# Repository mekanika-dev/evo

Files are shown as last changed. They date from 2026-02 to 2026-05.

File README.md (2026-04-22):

# Evo CNC

> Evo is a versatile CNC milling machine that lets you explore different materials. Fast and easy to use, it's the ideal choice for hobbyists and occasional professionals.

- [Assembly Guide & Documentation](https://support.mekanika.io/products/evo-cnc)
- [Shop](https://www.mekanika.io/en/store/be/evo/)
- [Contact](https://www.mekanika.io/contact-us/)

Evo CNC Milling Machine

## Repository Structure

- **`bom/`** - Bill of Materials
- **`cad/`** - CAD files
- **`docs/`** - Documentation files

The Bill of Materials is available as a CSV file, which is dynamically updated from our ERP. We recommend using this **[web viewer](https://mekanika-dev.github.io/data-sync-actions/odoo/bom-viewer.html)** to browse its content.

All 3D assembly files are made in STEP format and compatible with many CAD software. Please note that you will need Git LFS installed to clone or pull the repo correctly, since these files exceed 100MB.

## Assembly Guide

The assembly guide is available on our [support website](https://support.mekanika.io/products/evo-cnc). If you have feedback or want to raise an issue about a specific assembly step, you can use the feedback buttons available on each step's page.

The design files can also be viewed in web browsers using these links:

- [Evo S](https://a360.co/3XHU1ST)
- [Evo M](https://a360.co/437BPmZ)
- [Evo L](https://a360.co/49noRHT)
- [Evo Control Unit](https://a360.co/45p6r7A)

## Community

Mekanika encourages collaborative design and innovation. We welcome:

- Designers and engineers to contribute
- Feedback on design variations
- Any discussions around or products and potential improvements

Don't hesitate to join us on our [Discord](https://discord.gg/n7RsBtUdGc)

## License

This project is licensed under the **CERN Open Hardware Licence Version 2 - Strongly Reciprocal** ([CERN-OHL-S v2](https://ohwr.org/cern_ohl_s_v2.pdf))

For the complete license terms, see REUSE.toml

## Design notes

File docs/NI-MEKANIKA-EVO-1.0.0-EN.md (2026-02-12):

---
title: "USER MANUAL: CNC EVO"
css: style.css
---

<div class="cover-page" style="text-align: center;">

Logo Mekanika

<h4 style="margin-bottom: 0;">3-AXIS CNC MILLING MACHINE</h4>

<hr style="width: 200px; margin: 10px auto; color:#000 !important;"/>

<h4 style="margin-top: 0;">EVO MODEL V1.0</h4>

Evo ISO View

**ORIGINAL MANUAL**
<br/>
Version: 1.0.0-EN
<br/>
Revision Date: November 2025

</div>

## TABLE OF CONTENTS

#### 1. GENERAL INFORMATION

<ul style="list-style-type: none;">
  <li>1.1 <a href="#11-manufacturer-identification">Manufacturer identification</a></li>
  <li>1.2 <a href="#12-ce-declaration-of-conformity">CE Declaration of Conformity</a></li>
  <li>1.3 <a href="#13-intended-use">Intended use</a>
    <ul style="list-style-type: none;">
      <li>1.3.1 <a href="#131-normal-use">Normal Use</a></li>
      <li>1.3.2 <a href="#132-prohibited-uses">Prohibited Uses</a></li>
    </ul>
  </li>
  <li>1.4 <a href="#14-authorized-personnel">Authorized personnel</a>
    <ul style="list-style-type: none;">
      <li>1.4.1 <a href="#141-minimum-requirements">Minimum requirements</a></li>
      <li>1.4.2 <a href="#142-restrictions">Restrictions</a></li>
    </ul>
  </li>
</ul>

#### 2. SAFETY

<ul style="list-style-type: none;">
  <li>2.1 <a href="#21-safety-instructions-by-risk-level">Safety instructions by risk level</a></li>
  <li>2.2 <a href="#22-personal-protective-equipment">Personal protective equipment</a>
    <ul style="list-style-type: none;">
      <li>2.2.1 <a href="#221-mandatory-ppe">Mandatory PPE</a></li>
      <li>2.2.2 <a href="#222-dress-code">Dress code</a></li>
    </ul>
  </li>
  <li>2.3 <a href="#23-safety-devices">Safety devices</a>
    <ul style="list-style-type: none;">
      <li>2.3.1 <a href="#231-emergency-stop">Emergency stop</a></li>
      <li>2.3.2 <a href="#232-limit-switches">Limit switches</a></li>
      <li>2.3.3 <a href="#233-dust-shoe">Dust shoe</a></li>
    </ul>
  </li>
</ul>

#### 3. TECHNICAL DESCRIPTION

<ul style="list-style-type: none;">
  <li>3.1 <a href="#31-overview">Overview</a>
    <ul style="list-style-type: none;">
      <li>3.1.1 <a href="#311-axis-diagram">Axis diagram</a></li>
      <li>3.1.2 <a href="#312-control-box-diagram">Control box diagram</a></li>
    </ul>
  </li>
  <li>3.2 <a href="#32-technical-specifications">Technical specifications</a></li>
</ul>

#### 4. INSTALLATION & ASSEMBLY

<ul style="list-style-type: none;">
  <li>4.1 <a href="#41-unpacking-and-inspection">Unpacking and inspection</a>
    <ul style="list-style-type: none;">
      <li>4.1.1 <a href="#411-upon-receipt">Upon receipt</a></li>
      <li>4.1.2 <a href="#412-kit-inventory">Kit inventory</a></li>
    </ul>
  </li>
  <li>4.2 <a href="#42-assembly">Assembly</a>
    <ul style="list-style-type: none;">
      <li>4.2.1 <a href="#421-preparation">Preparation</a></li>
    </ul>
  </li>
  <li>4.3 <a href="#43-installation">Installation</a>
    <ul style="list-style-type: none;">
      <li>4.3.1 <a href="#431-recommended-layout">Recommended layout</a></li>
      <li>4.3.2 <a href="#432-facility-requirements">Facility requirements</a></li>
    </ul>
  </li>
</ul>

#### 5. INITIAL STARTUP

<ul style="list-style-type: none;">
  <li>5.1 <a href="#51-preliminary-checks">Preliminary checks</a>
    <ul style="list-style-type: none;">
      <li>5.1.1 <a href="#511-safety-checklist">Safety checklist</a></li>
    </ul>
  </li>
  <li>5.2 <a href="#52-first-power-on">First power-on</a>
    <ul style="list-style-type: none;">
      <li>5.2.1 <a href="#521-startup-sequence">Startup sequence</a></li>
    </ul>
  </li>
  <li>5.3 <a href="#53-functionality-test">Functionality test</a></li>
</ul>

#### 6. OPERATION

<ul style="list-style-type: none;">
  <li>6.1 <a href="#61-checklist-for-safe-machine-operation">Checklist for safe machine operation</a>
    <ul style="list-style-type: none;">
      <li>6.1.1 <a href="#611-daily-startup">Daily startup</a></li>
    </ul>
  </li>
  <li>6.2 <a href="#62-workpiece-clamping">Workpiece clamping</a>
    <ul style="list-style-type: none;">
      <li>6.2.1 <a href="#621-clamping-systems-provided-with-the-base-kit">Clamping systems provided with the base kit</a></li>
      <li>6.2.2 <a href="#622-clamping-rules">Clamping rules</a></li>
    </ul>
  </li>
  <li>6.3 <a href="#63-tool-installation">Tool installation</a>
    <ul style="list-style-type: none;">
      <li>6.3.1 <a href="#631-tool-change">Tool change</a></li>
      <li>6.3.2 <a href="#632-tool-length-measurement">Tool length measurement</a></li>
    </ul>
  </li>
  <li>6.4 <a href="#64-programming-and-milling">Programming and milling</a>
    <ul style="list-style-type: none;">
      <li>6.4.1 <a href="#641-accepted-formats">Accepted formats</a></li>
      <li>6.4.2 <a href="#642-operating-modes">Operating modes</a></li>
    </ul>
  </li>
  <li>6.5 <a href="#65-monitoring-during-milling">Monitoring during milling</a>
    <ul style="list-style-type: none;">
      <li>6.5.1 <a href="#651-control-points">Control points</a></li>
      <li>6.5.2 <a href="#652-anomalies-and-actions">Anomalies and actions</a></li>
    </ul>
  </li>
</ul>

#### 7. ADD-ONS AND OPTIONS

<ul style="list-style-type: none;">
  <li>7.1 <a href="#71-vacuum-table">Vacuum table</a>
    <ul style="list-style-type: none;">
      <li>7.1.1 <a href="#711-specifications">Specifications</a></li>
      <li>7.1.2 <a href="#712-use">Use</a></li>
    </ul>
  </li>
  <li>7.2 <a href="#72-dust-collection-kit">Dust collection kit</a>
    <ul style="list-style-type: none;">
      <li>7.2.1 <a href="#721-specifications">Specifications</a></li>
    </ul>
  </li>
  <li>7.3 <a href="#73-laser-module-lsr">Laser module (LSR)</a>
    <ul style="list-style-type: none;">
      <li>7.3.1 <a href="#731-specifications">Specifications</a></li>
    </ul>
  </li>
</ul>

#### 8. MAINTENANCE & TROUBLESHOOTING

<ul style="list-style-type: none;">
  <li>8.1 <a href="#81-preventive-maintenance-plan">Preventive maintenance plan</a></li>
  <li>8.2 <a href="#82-lubrication">Lubrication</a></li>
  <li>8.3 <a href="#83-spare-parts">Spare parts</a></li>
</ul>

#### 9. TROUBLESHOOTING

<ul style="list-style-type: none;">
  <li>9.1 <a href="#91-troubleshooting-and-diagnostics">Troubleshooting and diagnostics</a></li>
  <li>9.2 <a href="#92-technical-support">Technical support</a>
    <ul style="list-style-type: none;">
      <li>9.2.1 <a href="#921-before-contacting-support">Before contacting support</a></li>
    </ul>
  </li>
</ul>

#### 10. TRANSPORTATION & STORAGE

<ul style="list-style-type: none;">
  <li>10.1 <a href="#101-machine-transportation">Machine transportation</a></li>
  <li>10.2 <a href="#102-packaging--waste">Packaging & Waste</a></li>
  <li>10.3 <a href="#103-storage">Storage</a></li>
</ul>

## 1. GENERAL INFORMATION {#1-general-information}

### 1.1 Manufacturer identification {#11-manufacturer-identification}

**Mekanika SRL**

Chaussée de Mons 1281  
1070 Anderlecht, Belgium  
VAT No.: BE0740501760

**Contact:**

<ul style="list-style-type: none;">
<li><i class="fas fa-envelope" style="color: #2196f3;"></i> info@mekanika.io</li>
<li><i class="fas fa-globe" style="color: #2196f3;"></i> www.mekanika.io</a></li>
</ul>

### 1.2 CE Declaration of Conformity {#12-ce-declaration-of-conformity}

This machine complies with the following European directives:

- **2006/42/EC** - Machinery Directive
- **2014/30/EU** - Electromagnetic Compatibility (EMC) Directive

**Applied harmonized standards:**

- **EN ISO 12100:2010** - Safety of machinery, General principles
- **EN 60204-1:2006** - Electrical safety of machines
- **EN ISO 13850:2015** - Emergency stop function
- **EN 848-3:2012** - Safety of woodworking machines (partially)
- **EN 61000-6-1** - EMC Immunity
- **EN 61000-6-3** - EMC Emissions

The original declaration of conformity is provided with this machine.

### 1.3 Intended use {#13-intended-use}

Please read this user manual and all accompanying documents in their entirety before commissioning the machine.

If in doubt or if you need additional information, please do not hesitate to contact us before using the machine.

#### 1.3.1 Normal Use {#131-normal-use}

The MEKANIKA EVO CNC milling machine is a 3-axis CNC machine designed for:

<ul style="list-style-type: none; margin-left: 0.75em">
  <li><i class="fas fa-square-check" style="color: #4EBD7D;"></i> Milling wood and wood-based materials (plywood, MDF, OSB)</li>
  <li><i class="fas fa-square-check" style="color: #4EBD7D;"></i> Milling plastics (PVC, acrylic, polycarbonate)</li>
  <li><i class="fas fa-square-check" style="color: #4EBD7D;"></i> Milling non-ferrous metals (aluminum, brass)</li>
  <li><i class="fas fa-square-check" style="color: #4EBD7D;"></i> Milling composite materials (with special precautions)</li>
</ul>

#### 1.3.2 Prohibited Uses {#132-prohibited-uses}

The following uses are **PROHIBITED**:

<ul style="list-style-type: none; margin-left: 0.75em">
  <li><i class="fas fa-xmark" style="color: #d32f2f;"></i> Milling unknown composite materials or materials containing asbestos</li>
  <li><i class="fas fa-xmark" style="color: #d32f2f;"></i> Use in explosive atmospheres</li>
  <li><i class="fas fa-xmark" style="color: #d32f2f;"></i> Outdoor use or use in humid environments</li>
  <li><i class="fas fa-xmark" style="color: #d32f2f;"></i> Milling improperly secured workpieces</li>
  <li><i class="fas fa-xmark" style="color: #d32f2f;"></i> Milling beyond the machine's technical capabilities</li>
</ul>

### 1.4 Authorized personnel {#14-authorized-personnel}

#### 1.4.1 Minimum requirements {#141-minimum-requirements}

- **Minimum age:** 16 years
- **Required training:**
  - Complete reading of this manual
  - Completion of online training (series of free video tutorials)
  - Basic knowledge of CAM
- **Physical abilities:**
  - Normal or corrected vision
  - Normal or aided hearing
  - Sufficient mobility to access the emergency stop

#### 1.4.2 Restrictions {#142-restrictions}

- Prohibited for untrained persons
- Prohibited for persons under the influence (alcohol, drugs, medication)
- Mandatory supervision for persons learning to use the machine

## 2. SAFETY {#2-safety}

Read the entire user manual to familiarize yourself with the machine's features and how to use them. Improper operation of the machine can result in damage to the machine, your personal property, and cause serious injury, electric shock, and/or fire.

**It is imperative to comply with the safety instructions listed in this user manual at all times.**

### 2.1 Safety instructions by risk level {#21-safety-instructions-by-risk-level}

The following terms are used in this user manual to indicate different levels of potential hazard when using this machine. Safety symbols and their explanations require your attention.

Safety warnings do not eliminate any hazard. The instructions or warnings they provide are not a substitute for appropriate preventive measures.

> **<i class="fas fa-ban" style="color: #d32f2f;"></i> DANGER** - _Instructions which, if not properly followed, create a probability of property damage, collateral damage, serious injury or death, or create a high probability of minor injury._

| **RISK TYPE** | **SAFETY INSTRUCTIONS** |
| :--- | :--- |
| **Electrocution risk** | Machine plugs must match the power outlet used. Never modify the plug in any way. Do not use adapter plugs with grounded machines. |
| **Electrocution risk - indirect contact** | An insulation fault can energize normally non-conductive metal parts (chassis, frame, enclosure). Causes include: cable wear in cable chains, moisture infiltration, conductive dust accumulation, component failure, or mechanical damage. Never use the machine if: <br/> - The circuit breaker trips repeatedly; <br/> - Electrical arc traces are visible (blackening, burnt smell); <br/> - Moisture/condensation is visible in the enclosure. |
| **Toxic dust** | Some dusts created during milling of certain types of materials may contain chemicals known to cause cancer, birth defects, or other reproductive harm. Always inform yourself about the material you have at hand before milling it. Here are some examples of these chemicals: lead from non-ferrous metals containing lead, carbonate from carbon fiber, arsenic and chromium from chemically treated wood.<br><br>The risk you face from exposure varies depending on how often you perform this type of work. To reduce your exposure to these chemicals: work in a well-ventilated area and use approved safety equipment, such as dust masks specifically designed to filter microscopic particles. |
| **Explosive atmosphere** | Do not operate the machine in explosive atmospheres, for example in the presence of flammable liquids, gases, or dusts. Machines can create sparks that can ignite dust or fumes. |

> **<i class="fas fa-exclamation-triangle" style="color: #ff9800;"></i> WARNING** - _Instructions which, if not properly followed, create a probability of property damage and a possibility of serious injury._

| **RISK TYPE** | **SAFETY INSTRUCTIONS** |
| :--- | :--- |
| **Dress code** | Dress appropriately. Do not wear loose clothing or jewelry. Pin your hair above your shoulders so it cannot get caught in linear guides or moving parts. |
| **Vigilance** | Stay alert, watch what you are doing, and use common sense when operating a machine. Do not use a machine when you are tired and/or under the influence of drugs, alcohol, or medication. A moment of inattention when using a machine can result in serious injury. |
| **Personal protection** | Use personal protective equipment. Always wear eye protection. Protective equipment, such as a dust mask or appropriate hearing protection, reduces the risk of injury. |
| **Machine control** | This machine is controlled by a computer. During operation, it cannot be controlled directly. Lack of caution or expertise as well as program errors can cause unexpected movements. |
| **Rotating tool** | Do not touch the rotating tool area. The proximity of the rotating tool to your hand is not always easy to detect. |
| **Tool jam** | If the workpiece or end mill jams, immediately press the emergency stop button. Wait until all moving parts have stopped and the spindle is off, then release the jammed material. Do not try to do this while the spindle is running. |
| **Hot tools** | Do not touch the end mill or collet after use. After use, they are too hot to touch with bare hands. |
| **Hot surfaces** | Do not touch the motors as they can heat up during machine operation. |
| **Tool handling** | Be careful when handling tools, they can be very sharp. Never put any part of the tool or accessories in your mouth as this can cause serious injury. |
| **Workpiece clamping** | Before starting any milling operation, always secure your workpiece properly. Never try to hold the workpiece by hand or with accessories. These tools can easily jam in the material and can kick back, resulting in loss of control and serious injury. |
| **Limit sensors** | Never try to reach the limit sensors when the machine is moving, as this could result in your hand or fingers being crushed. |
| **Prohibited modifications** | Do not modify your machine, or use it in a manner not intended by the manufacturer. Any alteration or modification constitutes misuse and can result in serious injury. |
| **Lockout** | Disconnect the plug from the power source before making adjustments, changing accessories, or disassembling the machine. |
| **Machine access** | Keep the machine out of reach of children and do not allow persons unfamiliar with these instructions to use the machine. Machines are dangerous in the hands of untrained users. |
| **Safety distance** | Keep children and bystanders at a distance. Distractions can cause you to lose control and cause accidents. |

> **<i class="fas fa-info-circle" style="color: #2196f3;"></i> CAUTION** - _Instructions which, if not properly followed, create a possibility of property damage and a possibility of minor injury._

| **RISK TYPE** | **SAFETY INSTRUCTIONS** |
| :--- | :--- |
| **Mandatory training** | All persons using the machine must have read and fully understood all relevant safety and operating instructions. Any misunderstanding can result in injury. |
| **Cleanliness and lighting** | Keep the work area clean and well lit. Cluttered or dark areas are conducive to accidents. |
| **Indoor use** | Operate the machine only in indoor spaces. |
| **Moisture protection** | Do not expose the machine to moisture. The machine can only be used indoors. |
| **Supervision** | Do not leave the machine running unattended, and cut the spindle power if you leave. The machine is only secured when it is completely stopped and disconnected from the mains. |
| **Proper use** | Use the machine and its accessories in accordance with this manual, taking into account the working conditions and the work to be performed. Using the machine for operations other than those intended may result in a dangerous situation with a high probability of injury. |
| **Tool condition** | Never use dull or damaged end mills. Damaged end mills can break during use. Dull end mills require more force to cut, which can result in end mill breakage. |
| **Milling parameters** | The speed and feed rate of the end mill during engraving, contouring, or cutting are very important. Always respect the recommended speed and feed rate for a particular end mill/machine/operation configuration. |
| **Ventilation** | Remember to clean the ventilation openings of the control boxes using compressed air. Excessive dust accumulation inside the boxes can cause electrical failures. |
| **Preventive maintenance** | Properly maintain the tools you use. Check for misalignment or binding of moving parts, broken parts, and any other condition that may affect machine operation. If damaged, have the machine repaired before use. Many accidents are caused by poorly maintained machines. |
| **Repairs** | Have your machine repaired by a qualified technician using only identical replacement parts. |

### 2.2 Personal protective equipment {#22-personal-protective-equipment}

#### 2.2.1 Mandatory PPE {#221-mandatory-ppe}

| Equipment | Usage | Pictogram |
| :--- | :--- | :---: |
| **Safety glasses** | Recommended during milling | Safety glasses |
| **Hearing protection** | Recommended during milling, mandatory if noise level > 80 dB(A) | Hearing protection |
| **Gloves** | Recommended when handling workpieces/tools | Gloves |
| **FFP2 mask** | Mandatory when milling composite materials | FFP2 mask |
| **Safety shoes** | Recommended for any work in front of a machine | Safety shoes |

#### 2.2.2 Dress code {#222-dress-code}

**<i class="fas fa-square-check" style="color: #4EBD7D;"></i> MANDATORY:**

- Fitted clothing
- Short sleeves or rolled up
- Long hair tied back or under a cap

**<i class="fas fa-xmark" style="color: #d32f2f;"></i> PROHIBITED:**

- Jewelry (rings, necklaces, bracelets)
- Loose clothing
- Ties, scarves
- Gloves during milling

### 2.3 Safety devices {#23-safety-devices}

#### 2.3.1 Emergency stop {#231-emergency-stop}

**Characteristics:**

- Type: Lockable push button
- Color: Red on yellow background
- Standard: EN ISO 13850:2015
- Position: Front face, easily accessible

**Operation:**

1. **Activation:** Press the red button
   - Immediate stop of all movements
   - Spindle shutdown
   - Machine control software lockout
2. **Reset:** Turn the button clockwise
   - The program must be restarted manually

#### 2.3.2 Limit switches {#232-limit-switches}

**Configuration:**

- 4 mechanical NC limit switches

**Triple function:**

1. **Homing:** Machine referencing at startup
2. **Safety:** Emergency stop if limit reached
3. **Square gantry:** Gantry squaring

#### 2.3.3 Dust shoe {#233-dust-shoe}

**Dual function:**

- Protection against tool access
- Chip and dust extraction

> **<i class="fas fa-info-circle" style="color: #2196f3;"></i> CAUTION** - _Never remove the dust shoe during milling_

## 3. TECHNICAL DESCRIPTION {#3-technical-description}

### 3.1 Overview {#31-overview}

The MEKANIKA EVO is a 3-axis CNC milling machine, allowing material to be machined by moving along the X, Y, and Z axes, or a combination thereof by linear interpolation.

#### 3.1.1 Axis diagram {#311-axis-diagram}

Axis diagram

**Axis terminology:**

- **X-axis:** Lateral movement (left-right)
- **Y-axis:** Longitudinal movement (front-back)
- **Z-axis:** Vertical movement (up-down)

#### 3.1.2 Control box diagram {#312-control-box-diagram}

Control box diagram

**Connector description:**

- **1**: Fan
- **2**: Motors
- **3**: Limit switches
- **4**: Emergency stop
- **5**: Tool probe (Input 1)
- **6**: Spindle control
- **7**: Input 2
- **8**: Input 3
- **9**: Laser control
- **10**: HDMI
- **11**: USB 2.0
- **12**: Ethernet
- **13**: Power supply
- **14**: Ground

### 3.2 Technical specifications {#32-technical-specifications}

| **SPECIFICATION** | **VALUE** |
| :--- | :--- |
| **MACHINE DIMENSIONS** | |
| Overall dimensions | - S: 850 x 850 x 650 mm <br/> - M: 850 x 1250 x 650 mm <br/> - L: 1250 x 1250 x 650 mm |
| Total weight | - S: 37 kg <br/> - M: 42 kg <br/> - L: 48 kg |
| **WORK AREA** | |
| Milling surface | - S: 630 x 630 mm <br/> - M: 630 x 1030 mm <br/> - L: 1030 x 1030 mm |
| Table-spindle distance (max) | 110 mm |
| **PERFORMANCE** | |
| Max travel speed | 20000 mm/min |
| Recommended milling speed | 100 - 3500 mm/min |
| **MECHANICS** | |
| Linear guides | 24mm POM wheels & V-slot profiles |
| X,Y transmission | GT2 belt (steel reinforced) & GT2 pulley 20 teeth |
| Z transmission | T8 trapezoidal screw + Anti-backlash nut |
| Structure | Aluminum profiles + steel plates |
| **MOTORS** | |
| X,Y & Z motors | NEMA23 3A |
| **SPINDLE** | |
| Power | 1.4 kW |
| Cooling | Air |
| Rotation speed | 3000 - 25000 RPM |
| Collet | ER16 (1-11 mm) |
| Control | Voltage controller |
| **ELECTRICAL** | |
| Power supply | 230V AC single phase, 50 Hz |
| Maximum power | 1.8 kW |
| Protection | 16A fuse, mandatory ground |
| **ENVIRONMENT** | |
| Operating temperature | 5°C to 35°C |
| Relative humidity | 40-60% |
| Use | Indoor only |

## 4. INSTALLATION & ASSEMBLY {#4-installation--assembly}

### 4.1 Unpacking and inspection {#41-unpacking-and-inspection}

#### 4.1.1 Upon receipt {#411-upon-receipt}

**Check immediately:**

1. Condition of packaging (photos if damaged)
2. Presence of all packages (see delivery note)
3. Absence of visible damage

#### 4.1.2 Kit inventory {#412-kit-inventory}

We strongly recommend that you inventory your kit before starting assembly. The list of parts grouped by package is available on our website:
<br>
<i class="fas fa-globe" style="color: #2196f3;"></i> [support.mekanika.io/products/evo-cnc/kit-content](https://support.mekanika.io/products/evo-cnc/kit-content)

### 4.2 Assembly {#42-assembly}

Please carefully follow our online assembly guide to properly assemble your Mekanika machine.
<br>
<i class="fas fa-globe" style="color: #2196f3;"></i> [https://support.mekanika.io/products/evo-cnc/assembly-guide](https://support.mekanika.io/products/evo-cnc/assembly-guide)

#### 4.2.1 Preparation {#421-preparation}

- **Required space:**
  - S: 1.85 × 1.85 m minimum
  - M: 2.25 x 1.85 m minimum
  - L: 2.25 x 2.25 m minimum
- **Estimated time:** 8 hours (alone) - 5 hours (2 people)
- **Required tools:** Provided in the kit

> **<i class="fas fa-exclamation-triangle" style="color: #ff9800;"></i> WARNING** - There is a non-negligible risk of heavy parts falling during assembly. Please handle heavy parts with a minimum of 2 people.

> **<i class="fas fa-info-circle" style="color: #2196f3;"></i> CAUTION** - Please follow the precise order of assembly steps to avoid risks of machine malfunction.

### 4.3 Installation {#43-installation}

#### 4.3.1 Recommended layout {#431-recommended-layout}

If you have the "table stand" accessory, place the machine on a level and stable floor.
If you do not have a "table stand", place the machine on a sturdy and stable table allowing you to work at a comfortable height. To ensure a comfortable working height, we recommend a working height of approximately 85 cm.

All moving parts of the machine must be able to operate without collision.

The machine must be easily accessible and usable. In particular, the emergency stop button must be easily accessible at all times.

**Zone description:**

- **1**: Operating zone
- **2**: Loading zone
- **3**: Maintenance and safety zone

Work area

#### 4.3.2 Facility requirements {#432-facility-requirements}

**Floor:**

- Flatness: < 5 mm/m
- Capacity: > 200 kg/m²
- Type: Concrete (recommended)

**Environment:**

- Temperature: 18-25°C ideal
- Humidity: 40-60%
- Lighting: > 500 lux on work area
- Ventilation: Adequate air renewal

## 5. INITIAL STARTUP {#5-initial-startup}

Before commissioning, the machine and all connected components must be properly wired and in perfect condition.

The operator must have read and understood the complete documentation for the machine model concerned and the corresponding instructions. In addition, they must have been trained in the operation of the machine and its accessories and must be familiar with the use of CNC milling machines and PlanetCNC software in general.

### 5.1 Preliminary checks {#51-preliminary-checks}

> **<i class="fas fa-info-circle" style="color: #2196f3;"></i> CAUTION** - Never power on before these checks

#### 5.1.1 Safety checklist {#511-safety-checklist}

**Mechanical:**

<ul style="list-style-type: none; margin-left: 0.75em">
  <li><i class="fas fa-square-check" style="color: #4EBD7D;"></i> All fasteners tightened</li>
  <li><i class="fas fa-square-check" style="color: #4EBD7D;"></i> Freedom of axis movement</li>
  <li><i class="fas fa-square-check" style="color: #4EBD7D;"></i> No abnormal play</li>
  <li><i class="fas fa-square-check" style="color: #4EBD7D;"></i> Wheels tightened and belts tensioned</li>
</ul>

**Electrical:**

<ul style="list-style-type: none; margin-left: 0.75em">
  <li><i class="fas fa-square-check" style="color: #4EBD7D; "></i> Ground continuity (< 0.1 Ω)</li>
  <li><i class="fas fa-square-check" style="color: #4EBD7D;"></i> Cable insulation</li>
  <li><i class="fas fa-square-check" style="color: #4EBD7D;"></i> Tight connections</li>
  <li><i class="fas fa-square-check" style="color: #4EBD7D;"></i> Circuit breaker tested</li>
</ul>

**Safety:**

<ul style="list-style-type: none; margin-left: 0.75em">
  <li><i class="fas fa-square-check" style="color: #4EBD7D;"></i> Emergency stop accessible and functional</li>
  <li><i class="fas fa-square-check" style="color: #4EBD7D;"></i> Limit switches connected</li>
  <li><i class="fas fa-square-check" style="color: #4EBD7D;"></i> Dust shoe installed</li>
  <li><i class="fas fa-square-check" style="color: #4EBD7D;"></i> Work area clear</li>
</ul>

### 5.2 First power-on {#52-first-power-on}

#### 5.2.1 Startup sequence {#521-startup-sequence}

**1. Preparation**

- Clear area in front of and around the machine
- PPE worn
- Documentation within reach

**2. Power-on**

- Check that emergency stop is unlocked
- Turn on control box
- Wait for Raspberry Pi initialization
- Wait for PlanetCNC launch

**3. Initial checks**

- Control box fans rotating
- Touch screen on and PlanetCNC interface active
- Emergency stop button functional

### 5.3 Functionality test {#53-functionality-test}

We strongly recommend following our illustrated machine startup guide, available on our website:
<br>
<i class="fas fa-globe" style="color: #2196f3;"></i> [https://support.mekanika.io/products/evo-cnc/get-started](https://support.mekanika.io/products/evo-cnc/get-started)

This covers all the information necessary to test the machine on first use, as well as useful information on its operation and safety features.

## 6. OPERATION {#6-operation}

The Evo CNC milling machine is intended for occasional and semi-professional use. The machine's design allows for processing a wide variety of different materials, such as wood and non-ferrous metals. However, feed rates and tool engagement will remain modest.

The plausible and reasonable scope of uses includes:

- Manual displacement mode, using a digital "jog" to move the machine along its 3 axes independently.
- Automatic positioning procedure, performed by the user by clicking a digital button. This procedure moves the machine sequentially on each of its axes in the following order: Z, X, Y, until it encounters the limit switches.
- Tool length measurement procedure, activated by the user by clicking a digital button. This procedure lowers the machine at reduced speed along its Z-axis until its tool makes contact with a removable sensor previously placed by the user.
- Normal operating mode, where the machine moves automatically according to machine language, called G-code, previously loaded by the user.
- Manual control mode using a terminal allowing the machine to move according to machine language, called G-code, entered directly by the user.

The plausible and reasonable scope of interventions includes:

- Manual movement of the machine to access certain areas.
- Calibration of the belt and wheel system using a 10mm flat wrench.
- Tool change on the spindle.
- Installation or removal of the dust shoe.
- Installation or removal of material to be milled.
- Starting, pausing, and stopping G-Code.
- Connection/disconnection of external machine cables.
- Opening cable chains to access the machine.

### 6.1 Checklist for safe machine operation {#61-checklist-for-safe-machine-operation}

#### 6.1.1 Daily startup {#611-daily-startup}

**1. Inspection and equipment**

- Inspect the equipment to ensure there are no obvious defects, damaged collets, dull or cracked tools
- Use appropriate PPE (glasses, helmet, ...)
- Tie back long hair and wear well-fitted clothing and roll up your sleeves to avoid snags

**2. Machine preparation**

- Check where the emergency stop button is located
- Never connect or disconnect cables from the electronic control box when the device is powered on
- Ensure that the workpiece is firmly and securely clamped
- Check that the end mill is well sharpened and firmly tightened in the spindle collet
- When handling or changing end mills, avoid touching the cutting edges
- Keep your hands free during manual adjustments

**3. During use**

- Never touch the machine when it is running and keep your hands away from any moving parts during milling
- Stay away from the machine when it is operational

**4. After milling**

- Use a brush or vacuum to clean chips from surfaces
- If V-slot profiles are dusty, blow them out with compressed air to keep them clean and not obstructed by chips
- Clean the floor and work area around the machine
- Clean and store personal protective equipment
- Mark any defective equipment and contact us if you encounter a problem

**5. Normal shutdown**

1. Complete current milling
2. Stop spindle
3. **Shut down Raspberry Pi** (clean shutdown)
4. Wait 30 seconds
5. Turn off control box

> **<i class="fas fa-info-circle" style="color: #2196f3;"></i> CAUTION** - Follow the order to avoid corruption of the Raspberry Pi SD card

**6. Emergency stop**

**In case of danger:**

1. **Press immediately** on the red button
2. Cut power if necessary
3. Analyze the situation
4. Correct the problem
5. Reset (turn the button)
6. Perform a homing procedure again

### 6.2 Workpiece clamping {#62-workpiece-clamping}

#### 6.2.1 Clamping systems provided with the base kit {#621-clamping-systems-provided-with-the-base-kit}

**Wood screws:**

- For soft materials
- Direct screwing into spoilboard
- Regular spacing

**Clamps with inserts:**

- For all materials
- M6 inserts in spoilboard

#### 6.2.2 Clamping rules {#622-clamping-rules}

**<i class="fas fa-square-check" style="color: #4EBD7D;"></i> BEST PRACTICES:**

- Minimum 4 clamping points
- Symmetrical distribution
- Verification before milling

**<i class="fas fa-xmark" style="color: #d32f2f;"></i> PROHIBITIONS:**

- Manual holding
- Adhesive alone
- Cantilevered workpiece
- Excessive clamping (deformation)

> **<i class="fas fa-ban" style="color: #d32f2f;"></i> DANGER** - During milling, NEVER hold the workpiece by hand

### 6.3 Tool installation {#63-tool-installation}

#### 6.3.1 Tool change {#631-tool-change}

**Procedure:**

1. Wait for complete stop or machine pause
2. Move Z-axis to high position
3. Unlock ER16 nut (wrenches provided)
4. Remove tool (gloves strongly recommended)
5. Insert new tool
6. Tighten firmly (without excess)

#### 6.3.2 Tool length measurement {#632-tool-length-measurement}

**With the provided tool probe:**

1. Place the probe on the workpiece or spoilboard (depending on the Z0 coordinate defined in the program)
2. Position the spindle above the probe
3. Press the tool length measurement icon
4. Slow automatic descent
5. Contact and memorization of the new Z0 position

### 6.4 Programming and milling {#64-programming-and-milling}

#### 6.4.1 Accepted formats {#641-accepted-formats}

- **G-code:** .nc, .ngc, .gcode
- **Generation:** Via any CAM software. Some examples:
  - Fusion 360 (recommended)
  - VCarve
  - FreeCAD
  - Others

#### 6.4.2 Operating modes {#642-operating-modes}

**Automatic mode:**

1. Load G-code file
2. Check simulation in PlanetCNC
3. Position workpiece origin (X0 Y0 Z0)
4. Start program (Start)

**Manual mode (JOG):**

- Movement by axes
- Variable speed (10-100%)
- Incremental movement possible (examples: 0.01, 0.1, 1, 10 mm)

**MDI mode:**

- Direct G-code command sending
- Sequence testing
- Precise positioning

### 6.5 Monitoring during milling {#65-monitoring-during-milling}

#### 6.5.1 Control points {#651-control-points}

- Abnormal vibrations
- Unusual noise
- Chip quality
- Temperature near tool
- Workpiece clamping

#### 6.5.2 Anomalies and actions {#652-anomalies-and-actions}

| Anomaly | Probable cause | Immediate action |
| :--- | :--- | :--- |
| **Vibrations** | Worn tool or improper cut settings | STOP → Check tool and parameters |
| **Smoke** | Worn tool or improper cut settings | EMERGENCY → Stop |
| **Loud noise** | Very worn or broken tool | EMERGENCY → Stop |
| **Moving piece** | Insufficient clamping | EMERGENCY → Stop |

> In case of doubt → **IMMEDIATE STOP**

## 7. ADD-ONS AND OPTIONS {#7-add-ons-and-options}

### 7.1 Vacuum table {#71-vacuum-table}

#### 7.1.1 Specifications {#711-specifications}

- Plastic plenum with dedicated spoilboard and integrated gaskets
- 3 to 5 independent zones (depending on machine size)
- Vacuum pump and connections
- Installation: 2 hours

#### 7.1.2 Use {#712-use}

**New clamping system for workpieces:**

1. Place workpiece on spoilboard
2. Open necessary zones
3. Activate vacuum pump
4. Check hold (manual test)

Information about the kit and assembly guide is available on our website:

<i class="fas fa-globe" style="color: #2196f3;"></i> [support.mekanika.io/products/vacuum-table/vacuum-table-evo-pro](https://support.mekanika.io/products/vacuum-table/vacuum-table-evo-pro)

We strongly recommend following our illustrated startup guide dedicated to the vacuum table.

### 7.2 Dust collection kit {#72-dust-collection-kit}

#### 7.2.1 Specifications {#721-specifications}

- Anti-static suction hose Ø100mm
- Compatible with most workshop vacuums
- Swivel tubular steel support
- Installation: 1 hour

Information about the kit and assembly guide is available on our website:

<i class="fas fa-globe" style="color: #2196f3;"></i> [support.mekanika.io/products/dust-collection-kit](https://support.mekanika.io/products/dust-collection-kit)

### 7.3 Laser module (LSR) {#73-laser-module-lsr}

#### 7.3.1 Specifications {#731-specifications}

- Model: PLH3D-XT-50
- Power: 6W optical
- Wavelength: 445 nm (blue)
- Laser class: 4

> **<i class="fas fa-ban" style="color: #d32f2f;"></i> DANGER - CLASS 4 LASER**
>
> **Dedicated documentation:** See separate manual provided with the machine

Information about the kit and assembly guide is available on our website:

<i class="fas fa-globe" style="color: #2196f3;"></i> [support.mekanika.io/products/laser-head-6w](https://support.mekanika.io/products/laser-head-6w)

## 8. MAINTENANCE & TROUBLESHOOTING {#8-maintenance--troubleshooting}

We strongly recommend following our video maintenance guide, available on our website:

<i class="fas fa-globe" style="color: #2196f3;"></i> [support.mekanika.io/products/evo-cnc/maintenance](https://support.mekanika.io/products/evo-cnc/maintenance)

### 8.1 Preventive maintenance plan {#81-preventive-maintenance-plan}

| **FREQUENCY** | **OPERATION** | **DURATION** | **MACHINE STOP** |
| :--- | :--- | :--- | :--- |
| **Daily** | Chip cleaning | 10 min | No |
| **Daily** | General visual inspection | 5 min | No |
| **Monthly** | Wheel tightening X Y Z | 15 min | Yes |
| **Monthly** | Z trapezoidal screw lubrication | 5 min | Yes |
| **Monthly** | Control box filter cleaning | 10 min | Yes |
| **Monthly** | Belt tension adjustment X Y | 20 min | Yes |
| **Monthly** | Z mechanical play check | 15 min | Yes |
| **Monthly** | Complete fastener check | 45 min | Yes |
| **Annual** | Complete machine overhaul | 4h | Yes |
| **Annual** | Possible bearing replacement | 2h | Yes |
| **Annual** | Geometric calibration | 2h | Yes |

### 8.2 Lubrication {#82-lubrication}

A linear system must be sufficiently lubricated to function properly and avoid excessive wear or overheating. The required lubrication interval is determined by environmental conditions.

In general, lubrication is necessary every 100 to 200 hours of operation. We recommend the use of lithium-based greases, which perform well in high-load applications and have good oxidation stability.

**Procedure:**

1. Clean before greasing (cloth and isopropyl alcohol)
2. Apply grease moderately
3. Perform 10 complete machine movement cycles
4. Wipe off excess grease

### 8.3 Spare parts {#83-spare-parts}

All machine and control box parts can be purchased individually as spare parts.

Please contact us directly about this.

When ordering spare parts, please provide information on the model, size, and part number of the machine available according to the construction instructions.

## 9. TROUBLESHOOTING {#9-troubleshooting}

### 9.1 Troubleshooting and diagnostics {#91-troubleshooting-and-diagnostics}

If you have a problem with your machine, please consult our troubleshooting guides available online:

<i class="fas fa-globe" style="color: #2196f3;"></i> [https://support.mekanika.io/products/evo-cnc/troubleshoot](https://support.mekanika.io/products/evo-cnc/troubleshoot)

### 9.2 Technical support {#92-technical-support}

#### 9.2.1 Before contacting support {#921-before-contacting-support}

**Information to prepare:**

- Machine model (EVO)
- Machine serial number (located under the control box)
- Order number
- Problem description
- Photos/videos if possible

#### **CONTACT FORM**

<i class="fas fa-globe" style="color: #2196f3;"></i> [www.mekanika.io/en/contact-support](https://www.mekanika.io/en/contact-support)

## 10. TRANSPORTATION & STORAGE {#10-transportation--storage}

### 10.1 Machine transportation {#101-machine-transportation}

If you wish to transport the machine, pay special attention to its dimensions and weight, you may need additional people for transport.

Never lift heavy loads above people.

Avoid unilateral loading of the machine chassis during transport.

### 10.2 Packaging & Waste {#102-packaging--waste}

If you do not wish to reuse the device packaging, please sort it according to local sorting rules and take it to a waste collection center for recycling.

If you need to replace certain machine components, or decommission it, please go to your local recycling center and sort selectively.

| **Material** | **Components** | **Stream** |
| :--- | :--- | :--- |
| **Aluminum** | Profile structure | Metal recycling |
| **Steel** | Connection plates, axes, fasteners | Metal recycling |
| **Electronics** | Control boards, motors | WEEE\* |
| **Cables** | Sheathed copper | WEEE\* |
| **Plastics** | Cable chains, connection plates | Plastic sorting |

\* _Waste Electrical and Electronic Equipment_

### 10.3 Storage {#103-storage}

If the machine or its components are not used for an extended period, please observe the following points regarding storage:

- Store the machine and its components only in closed rooms
- Protect the machine and its components from moisture, cold, heat, and direct sunlight
- Store the machine and its components away from dust and cover if necessary
- The storage location must not be subject to vibrations.

---

**END OF USER MANUAL**

This manual is the property of MEKANIKA SRL. Any reproduction, even partial, is prohibited without written authorization.
<br/>

**IMPORTANT NOTES:**

- This manual must remain with the machine
- In case of resale, transmit all documents
- Updates available at [support.mekanika.io/download-center/cnc-milling](www.mekanika.io/en/contact-support)
- For any questions: info@mekanika.io
  <br/>

**Keep this manual for future reference**

---

**© 2025 MEKANIKA SRL - All rights reserved**

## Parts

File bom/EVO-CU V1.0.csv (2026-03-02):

level | component_reference | component_name | component_quantity | parent_bom_reference | parent_bom_name | has_child_bom
0 | M00148 | EVO - Control Unit | 1.00 |  |  | True
1 | M00218 | CNC Evo/Pro - Steel Parts - Control Unit Base | 1.00 | M00148 | EVO - Control Unit | False
1 | M00219 | CNC Evo/Pro - Steel Parts - Control Unit Cover | 1.00 | M00148 | EVO - Control Unit | False
1 | M00367 | CNC USB Controller Mk3/4 | 1.00 | M00148 | EVO - Control Unit | False
1 | M00368 | CNC USB Controller license | 1.00 | M00148 | EVO - Control Unit | False
1 | M00663 | MicroSD 32GB Samsung Evo+ | 1.00 | M00148 | EVO - Control Unit | False
1 | M00750 | SMPS 360W 24V 15A (CNC Evo) | 1.00 | M00148 | EVO - Control Unit | False
1 | M00853 | USB-C 24V to 5V 3A converter | 1.00 | M00148 | EVO - Control Unit | False
1 | M00502 | Ethernet RJ45 female 50cm, panel mount | 1.00 | M00148 | EVO - Control Unit | False
1 | M00542 | HDMI (female) panel mount to micro HDMI (male) | 1.00 | M00148 | EVO - Control Unit | False
1 | M00852 | USB-A male to A female panel mount, 30cm | 3.00 | M00148 | EVO - Control Unit | False
1 | M01077 | GX12 male 3 pins aux 45cm, panel mount (Probe) | 1.00 | M00148 | EVO - Control Unit | False
1 | M00073 | Axial Fan 24V 60x60mm, panel mount | 1.00 | M00148 | EVO - Control Unit | False
1 | M00514 | Fan cover 60mm | 1.00 | M00148 | EVO - Control Unit | False
1 | M00865 | Wago 3 connectors | 3.00 | M00148 | EVO - Control Unit | False
1 | M00866 | Wago 5 connectors | 3.00 | M00148 | EVO - Control Unit | False
1 | M01071 | Rubber foot M4 - Flat with Rivet | 4.00 | M00148 | EVO - Control Unit | False
1 | M00837 | TFHC M4x35 Black screw | 2.00 | M00148 | EVO - Control Unit | False
1 | M00536 | GX12 male 2 pins aux 45cm, panel mount (Emergency Button) | 1.00 | M00148 | EVO - Control Unit | False
1 | M01715 | ISO 7380 M3x4 Black Screw | 24.00 | M00148 | EVO - Control Unit | False
1 | M00552 | Hex spacer M3x30 female/female | 2.00 | M00148 | EVO - Control Unit | False
1 | M00553 | Hex spacer M3x8 female/female | 6.00 | M00148 | EVO - Control Unit | False
1 | M00629 | Lock Nut DIN985 M4 | 8.00 | M00148 | EVO - Control Unit | False
1 | M01697 | DIN912 M4x12 Black screw | 6.00 | M00148 | EVO - Control Unit | False
1 | M01693 | ISO 7380 M3x10 Black Screw | 16.00 | M00148 | EVO - Control Unit | False
1 | M00739 | Raspberry Pi 4B 2G | 1.00 | M00148 | EVO - Control Unit | False
1 | M00984 | Female Banana Socket - Tab Termination | 1.00 | M00148 | EVO - Control Unit | False
1 | M00851 | USB-A USB-B cable 30cm Elbow type | 1.00 | M00148 | EVO - Control Unit | False
1 | M00107 | C14 Panel Mount 10A fuse | 1.00 | M00148 | EVO - Control Unit | False
1 | M00530 | Fuse T slow 10A | 1.00 | M00148 | EVO - Control Unit | False
1 | M00744 | Rocker switch DPST, panel mount | 1.00 | M00148 | EVO - Control Unit | False
1 | M00540 | GX12 male 5 pins output 45cm, panel mount (VFD, Laser) | 1.00 | M00148 | EVO - Control Unit | False
1 | M00537 | GX12 male 2 pins aux 45cm, panel mount (Safety Enclosure) | 2.00 | M00148 | EVO - Control Unit | False
1 | M00706 | Nylon Cap HP-22 | 2.00 | M00148 | EVO - Control Unit | False
1 | M01729 | Dust Filter Mesh ("M"), 7cmx7cmx0.375mm, 0.5mm aperture | 1.00 | M00148 | EVO - Control Unit | False
1 | M01777 | Diode Schottky - 40 V 1 A 2-Pin DO-204AL 1N5819 | 1.00 | M00148 | EVO - Control Unit | False
1 | M00949 | Motor Driver 2DM542-N - EVO | 4.00 | M00148 | EVO - Control Unit | False
1 | M00918 | XLR 4 pole female panel M3, Pre-wired 18cm breakout | 4.00 | M00148 | EVO - Control Unit | False
1 | M00559 | IDC Adapter PCB & Ribbon - 10-pin - 90° | 4.00 | M00148 | EVO - Control Unit | False
1 | M01070 | Insulated Crimp Bootlace Ferrule | 4.00 | M00148 | EVO - Control Unit | False
1 | M00620 | EVO - Limit Switches PCB Assembly | 1.00 | M00148 | EVO - Control Unit | True
2 | M00714 | PCB Custom for CNC Limit Switches | 1.00 | M00620 | EVO - Limit Switches PCB Assembly | False
2 | M00841 | ALL - Tapped XLR 3 pole female panel, vertical PCB | 4.00 | M00620 | EVO - Limit Switches PCB Assembly | True
3 | M00917 | XLR 3 pole female panel, vertical PCB | 4.00 | M00841 | ALL - Tapped XLR 3 pole female panel, vertical PCB | False
2 | M00790 | Screw 2 Way PCB Terminal Block 5mm Pitch | 1.00 | M00620 | EVO - Limit Switches PCB Assembly | False
2 | M00791 | Screwless 4 Way PCB Terminal Block 3.5mm Pitch | 1.00 | M00620 | EVO - Limit Switches PCB Assembly | False
1 | M00407 | Coloured Washer M3 - Blue | 2.00 | M00148 | EVO - Control Unit | False
1 | M00408 | Coloured Washer M3 - Green | 2.00 | M00148 | EVO - Control Unit | False
1 | M00409 | Coloured Washer M3 - Red | 2.00 | M00148 | EVO - Control Unit | False
1 | M00410 | Coloured Washer M3 - Yellow | 2.00 | M00148 | EVO - Control Unit | False
1 | M00718 | PWM to Analog Voltage Converter 0-10V | 1.00 | M00148 | EVO - Control Unit | False

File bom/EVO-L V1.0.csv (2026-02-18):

level | component_reference | component_name | component_quantity | parent_bom_reference | parent_bom_name | has_child_bom
0 | M00652 | EVO-L [M0 use] | 1.00 |  |  | True
1 | M00201 | EVO-L - Main Box 1/2 | 1.00 | M00652 | EVO-L [M0 use] | True
2 | M00148 | EVO - Control Unit | 1.00 | M00201 | EVO-L - Main Box 1/2 | True
3 | M00218 | CNC Evo/Pro - Steel Parts - Control Unit Base | 1.00 | M00148 | EVO - Control Unit | False
3 | M00219 | CNC Evo/Pro - Steel Parts - Control Unit Cover | 1.00 | M00148 | EVO - Control Unit | False
3 | M00367 | CNC USB Controller Mk3/4 | 1.00 | M00148 | EVO - Control Unit | False
3 | M00368 | CNC USB Controller license | 1.00 | M00148 | EVO - Control Unit | False
3 | M00663 | MicroSD 32GB Samsung Evo+ | 1.00 | M00148 | EVO - Control Unit | False
3 | M00750 | SMPS 360W 24V 15A (CNC Evo) | 1.00 | M00148 | EVO - Control Unit | False
3 | M00853 | USB-C 24V to 5V 3A converter | 1.00 | M00148 | EVO - Control Unit | False
3 | M00502 | Ethernet RJ45 female 50cm, panel mount | 1.00 | M00148 | EVO - Control Unit | False
3 | M00542 | HDMI (female) panel mount to micro HDMI (male) | 1.00 | M00148 | EVO - Control Unit | False
3 | M00852 | USB-A male to A female panel mount, 30cm | 3.00 | M00148 | EVO - Control Unit | False
3 | M01077 | GX12 male 3 pins aux 45cm, panel mount (Probe) | 1.00 | M00148 | EVO - Control Unit | False
3 | M00073 | Axial Fan 24V 60x60mm, panel mount | 1.00 | M00148 | EVO - Control Unit | False
3 | M00514 | Fan cover 60mm | 1.00 | M00148 | EVO - Control Unit | False
3 | M00865 | Wago 3 connectors | 3.00 | M00148 | EVO - Control Unit | False
3 | M00866 | Wago 5 connectors | 3.00 | M00148 | EVO - Control Unit | False
3 | M01071 | Rubber foot M4 - Flat with Rivet | 4.00 | M00148 | EVO - Control Unit | False
3 | M00837 | TFHC M4x35 Black screw | 2.00 | M00148 | EVO - Control Unit | False
3 | M00536 | GX12 male 2 pins aux 45cm, panel mount (Emergency Button) | 1.00 | M00148 | EVO - Control Unit | False
3 | M01715 | ISO 7380 M3x4 Black Screw | 24.00 | M00148 | EVO - Control Unit | False
3 | M00552 | Hex spacer M3x30 female/female | 2.00 | M00148 | EVO - Control Unit | False
3 | M00553 | Hex spacer M3x8 female/female | 6.00 | M00148 | EVO - Control Unit | False
3 | M00629 | Lock Nut DIN985 M4 | 8.00 | M00148 | EVO - Control Unit | False
3 | M01697 | DIN912 M4x12 Black screw | 6.00 | M00148 | EVO - Control Unit | False
3 | M01693 | ISO 7380 M3x10 Black Screw | 16.00 | M00148 | EVO - Control Unit | False
3 | M00739 | Raspberry Pi 4B 2G | 1.00 | M00148 | EVO - Control Unit | False
3 | M00984 | Female Banana Socket - Tab Termination | 1.00 | M00148 | EVO - Control Unit | False
3 | M00851 | USB-A USB-B cable 30cm Elbow type | 1.00 | M00148 | EVO - Control Unit | False
3 | M00107 | C14 Panel Mount 10A fuse | 1.00 | M00148 | EVO - Control Unit | False
3 | M00530 | Fuse T slow 10A | 1.00 | M00148 | EVO - Control Unit | False
3 | M00744 | Rocker switch DPST, panel mount | 1.00 | M00148 | EVO - Control Unit | False
3 | M00540 | GX12 male 5 pins output 45cm, panel mount (VFD, Laser) | 1.00 | M00148 | EVO - Control Unit | False
3 | M00537 | GX12 male 2 pins aux 45cm, panel mount (Safety Enclosure) | 2.00 | M00148 | EVO - Control Unit | False
3 | M00706 | Nylon Cap HP-22 | 2.00 | M00148 | EVO - Control Unit | False
3 | M01729 | Dust Filter Mesh ("M"), 7cmx7cmx0.375mm, 0.5mm aperture | 1.00 | M00148 | EVO - Control Unit | False
3 | M00949 | Motor Driver 2DM542-N - EVO | 4.00 | M00148 | EVO - Control Unit | False
3 | M00918 | XLR 4 pole female panel M3, Pre-wired 18cm breakout | 4.00 | M00148 | EVO - Control Unit | False
3 | M00559 | IDC Adapter PCB & Ribbon - 10-pin - 90° | 4.00 | M00148 | EVO - Control Unit | False
3 | M01070 | Insulated Crimp Bootlace Ferrule | 4.00 | M00148 | EVO - Control Unit | False
3 | M00620 | EVO - Limit Switches PCB Assembly | 1.00 | M00148 | EVO - Control Unit | True
4 | M00714 | PCB Custom for CNC Limit Switches | 1.00 | M00620 | EVO - Limit Switches PCB Assembly | False
4 | M00841 | ALL - Tapped XLR 3 pole female panel, vertical PCB | 4.00 | M00620 | EVO - Limit Switches PCB Assembly | True
5 | M00917 | XLR 3 pole female panel, vertical PCB | 4.00 | M00841 | ALL - Tapped XLR 3 pole female panel, vertical PCB | False
4 | M00790 | Screw 2 Way PCB Terminal Block 5mm Pitch | 1.00 | M00620 | EVO - Limit Switches PCB Assembly | False
4 | M00791 | Screwless 4 Way PCB Terminal Block 3.5mm Pitch | 1.00 | M00620 | EVO - Limit Switches PCB Assembly | False
3 | M00407 | Coloured Washer M3 - Blue | 2.00 | M00148 | EVO - Control Unit | False
3 | M00408 | Coloured Washer M3 - Green | 2.00 | M00148 | EVO - Control Unit | False
3 | M00409 | Coloured Washer M3 - Red | 2.00 | M00148 | EVO - Control Unit | False
3 | M00410 | Coloured Washer M3 - Yellow | 2.00 | M00148 | EVO - Control Unit | False
3 | M00718 | PWM to Analog Voltage Converter 0-10V | 1.00 | M00148 | EVO - Control Unit | False
2 | M00174 | EVO - Mechanical Elements Box | 1.00 | M00201 | EVO-L - Main Box 1/2 | True
3 | M00834 | T8 Lead Screw 250mm | 1.00 | M00174 | EVO - Mechanical Elements Box | False
3 | M00175 | EVO - Miscellaneous Components Bag | 1.00 | M00174 | EVO - Mechanical Elements Box | True
4 | M00380 | Cable Chain TP15 End Connector (Female) | 2.00 | M00175 | EVO - Miscellaneous Components Bag | False
4 | M00381 | Cable Chain TP15 End Connector (Male) | 2.00 | M00175 | EVO - Miscellaneous Components Bag | False
4 | M00706 | Nylon Cap HP-22 | 2.00 | M00175 | EVO - Miscellaneous Components Bag | False
4 | M01205 | EVO - Foot M6X40 10PA D30 + Anti slip, Ready-to-Use | 4.00 | M00175 | EVO - Miscellaneous Components Bag | True
5 | M00525 | Foot M6X40 10PA - 30mm + Anti slip | 4.00 | M01205 | EVO - Foot M6X40 10PA D30 + Anti slip, Ready-to-Use | False
4 | M00076 | Ball Bearing 608-2RS 8x22x7mm | 2.00 | M00175 | EVO - Miscellaneous Components Bag | False
4 | M00830 | Stop Ring M8 | 2.00 | M00175 | EVO - Miscellaneous Components Bag | False
4 | M00068 | Anti-backlash Nut for T8 Screw | 1.00 | M00175 | EVO - Miscellaneous Components Bag | False
4 | M00517 | Flexible Motor Coupler D20L25 - 6.35mm to 8mm | 1.00 | M00175 | EVO - Miscellaneous Components Bag | False
4 | M00389 | Cable Tie 100mm x 2.5 mm | 13.00 | M00175 | EVO - Miscellaneous Components Bag | False
4 | M00887 | Wood screw 4x25mm | 4.00 | M00175 | EVO - Miscellaneous Components Bag | False
4 | M00075 | B-Type Square Nut M6 | 6.00 | M00175 | EVO - Miscellaneous Components Bag | False
4 | M00531 | GT2 Pulley 20T, bore 6.35mm, belt width 6mm | 3.00 | M00175 | EVO - Miscellaneous Components Bag | False
4 | M00183 | CNC Evo - Steel Parts - Belt Tensioner | 6.00 | M00175 | EVO - Miscellaneous Components Bag | False
3 | M00176 | EVO - Mounting Tools Bag | 1.00 | M00174 | EVO - Mechanical Elements Box | True
4 | M00023 | Allen Key 2mm | 1.00 | M00176 | EVO - Mounting Tools Bag | False
4 | M00022 | Allen Key 2,5mm | 1.00 | M00176 | EVO - Mounting Tools Bag | False
4 | M00024 | Allen Key 3mm | 1.00 | M00176 | EVO - Mounting Tools Bag | False
4 | M00025 | Allen Key 4mm | 1.00 | M00176 | EVO - Mounting Tools Bag | False
4 | M00026 | Allen Key 5mm | 1.00 | M00176 | EVO - Mounting Tools Bag | False
4 | M00027 | Allen Key 6mm | 1.00 | M00176 | EVO - Mounting Tools Bag | False
4 | M00806 | Spanner 7mm | 1.00 | M00176 | EVO - Mounting Tools Bag | False
4 | M00807 | Spanner 8mm | 1.00 | M00176 | EVO - Mounting Tools Bag | False
4 | M00801 | Spanner 10mm | 1.00 | M00176 | EVO - Mounting Tools Bag | False
4 | M01676 | EVO - Acrylic Parts - Assembly Gauge | 1.00 | M00176 | EVO - Mounting Tools Bag | True
5 | M00716 | PMMA Sheet 3mm 600x400mm, Light Blue | 0.02 | M01676 | EVO - Acrylic Parts - Assembly Gauge | False
3 | M00142 | EVO - Acrylic & Steel Parts Bag | 1.00 | M00174 | EVO - Mechanical Elements Box | True
4 | M00184 | CNC Evo - Steel Parts - Cable Chain Support X | 1.00 | M00142 | EVO - Acrylic & Steel Parts Bag | False
4 | M00185 | CNC Evo - Steel Parts - Cable Chain Support Y1 Left | 1.00 | M00142 | EVO - Acrylic & Steel Parts Bag | False
4 | M00186 | CNC Evo - Steel Parts - Cable Chain Support Y1 Right | 1.00 | M00142 | EVO - Acrylic & Steel Parts Bag | False
4 | M01677 | EVO - Acrylic Parts - Bearing Support Z (Closed) | 2.00 | M00142 | EVO - Acrylic & Steel Parts Bag | True
5 | M00716 | PMMA Sheet 3mm 600x400mm, Light Blue | 0.04 | M01677 | EVO - Acrylic Parts - Bearing Support Z (Closed) | False
4 | M01678 | EVO - Acrylic Parts - Bearing Support Z (Open) | 2.00 | M00142 | EVO - Acrylic & Steel Parts Bag | True
5 | M00716 | PMMA Sheet 3mm 600x400mm, Light Blue | 0.04 | M01678 | EVO - Acrylic Parts - Bearing Support Z (Open) | False
4 | M01679 | EVO - Acrylic Parts - Limit Switches Support Y | 2.00 | M00142 | EVO - Acrylic & Steel Parts Bag | True
5 | M00716 | PMMA Sheet 3mm 600x400mm, Light Blue | 0.04 | M01679 | EVO - Acrylic Parts - Limit Switches Support Y | False
3 | M00164 | EVO - ISO7380 Black Screw Bag - M3x10 | 1.00 | M00174 | EVO - Mechanical Elements Box | True
4 | M01693 | ISO 7380 M3x10 Black Screw | 8.00 | M00164 | EVO - ISO7380 Black Screw Bag - M3x10 | False
3 | M00151 | EVO - DIN912 Black Screw Bag - M4x12 | 1.00 | M00174 | EVO - Mechanical Elements Box | True
4 | M01697 | DIN912 M4x12 Black screw | 17.00 | M00151 | EVO - DIN912 Black Screw Bag - M4x12 | False
3 | M00152 | EVO - DIN912 Black Screw Bag - M4x25 + M6x20 | 1.00 | M00174 | EVO - Mechanical Elements Box | True
4 | M00451 | DIN912 M6x20 Black screw | 1.00 | M00152 | EVO - DIN912 Black Screw Bag - M4x25 + M6x20 | False
4 | M01675 | DIN912 M4x25 Black screw | 1.00 | M00152 | EVO - DIN912 Black Screw Bag - M4x25 + M6x20 | False
3 | M00153 | EVO - DIN912 Black Screw Bag - M5x16 | 1.00 | M00174 | EVO - Mechanical Elements Box | True
4 | M00437 | DIN912 M5x16 Black screw | 9.00 | M00153 | EVO - DIN912 Black Screw Bag - M5x16 | False
3 | M00154 | EVO - DIN912 Black Screw Bag - M5x35 | 1.00 | M00174 | EVO - Mechanical Elements Box | True
4 | M00441 | DIN912 M5x35 Black screw | 9.00 | M00154 | EVO - DIN912 Black Screw Bag - M5x35 | False
3 | M00155 | EVO - DIN912 Black Screw Bag - M5x40 | 1.00 | M00174 | EVO - Mechanical Elements Box | True
4 | M00442 | DIN912 M5x40 Black screw | 4.00 | M00155 | EVO - DIN912 Black Screw Bag - M5x40 | False
3 | M00156 | EVO - DIN912 Black Screw Bag - M5x45 | 1.00 | M00174 | EVO - Mechanical Elements Box | True
4 | M00443 | DIN912 M5x45 Black screw | 11.00 | M00156 | EVO - DIN912 Black Screw Bag - M5x45 | False
3 | M00157 | EVO - DIN912 Black Screw Bag - M5x85 | 1.00 | M00174 | EVO - Mechanical Elements Box | True
4 | M00446 | DIN912 M5x85 Black screw | 8.00 | M00157 | EVO - DIN912 Black Screw Bag - M5x85 | False
3 | M00158 | EVO - DIN912 Black Screw Bag - M6x10 | 1.00 | M00174 | EVO - Mechanical Elements Box | True
4 | M01716 | DIN912 M6x10 Black screw | 13.00 | M00158 | EVO - DIN912 Black Screw Bag - M6x10 | False
3 | M00159 | EVO - DIN912 Black Screw Bag - M6x12 | 1.00 | M00174 | EVO - Mechanical Elements Box | True
4 | M01718 | DIN912 M6x12 Black screw | 23.00 | M00159 | EVO - DIN912 Black Screw Bag - M6x12 | False
3 | M00160 | EVO - DIN912 Black Screw Bag - M6x16 | 1.00 | M00174 | EVO - Mechanical Elements Box | True
4 | M01704 | DIN912 M6x16 Black screw | 62.00 | M00160 | EVO - DIN912 Black Screw Bag - M6x16 | False
3 | M00177 | EVO - DIN934 Nut Bag - M6 | 1.00 | M00174 | EVO - Mechanical Elements Box | True
4 | M00703 | Nut DIN934 M6 | 4.00 | M00177 | EVO - DIN934 Nut Bag - M6 | False
3 | M00165 | EVO - DIN985 Lock Nut Bag - M4 | 1.00 | M00174 | EVO - Mechanical Elements Box | True
4 | M00629 | Lock Nut DIN985 M4 | 6.00 | M00165 | EVO - DIN985 Lock Nut Bag - M4 | False
3 | M00161 | EVO - DIN985 Lock Nut Bag - M5 | 1.00 | M00174 | EVO - Mechanical Elements Box | True
4 | M00632 | Lock Nut DIN985 M5 | 42.00 | M00161 | EVO - DIN985 Lock Nut Bag - M5 | False
3 | M00162 | EVO - I-Type Sliding Nut Bag - M4 | 1.00 | M00174 | EVO - Mechanical Elements Box | True
4 | M00554 | I-Type Sliding Nut M4 | 10.00 | M00162 | EVO - I-Type Sliding Nut Bag - M4 | False
3 | M00163 | EVO - I-Type Sliding Nut Bag - M6 | 1.00 | M00174 | EVO - Mechanical Elements Box | True
4 | M00556 | I-Type Sliding Nut M6 | 63.00 | M00163 | EVO - I-Type Sliding Nut Bag - M6 | False
3 | M00150 | EVO - DIN9021 Washer Bag - M6x18 | 1.00 | M00174 | EVO - Mechanical Elements Box | True
4 | M01694 | DIN9021 Washer M6x18 | 31.00 | M00150 | EVO - DIN9021 Washer Bag - M6x18 | False
3 | M00149 | EVO - DIN125A Washer Bag - M6x12 | 1.00 | M00174 | EVO - Mechanical Elements Box | True
4 | M00419 | DIN125A M6x12 Washer | 10.00 | M00149 | EVO - DIN125A Washer Bag - M6x12 | False
3 | M00170 | EVO - Eccentric Spacer Bag - M5x6 | 1.00 | M00174 | EVO - Mechanical Elements Box | True
4 | M00481 | Eccentric Spacer M5 - 6mm | 15.00 | M00170 | EVO - Eccentric Spacer Bag - M5x6 | False
3 | M00171 | EVO - Spacer Bag - M5x6 | 1.00 | M00174 | EVO - Mechanical Elements Box | True
4 | M00798 | Spacer M5x6mm | 8.00 | M00171 | EVO - Spacer Bag - M5x6 | False
3 | M00172 | EVO - Spacer Bag - M5x9 | 1.00 | M00174 | EVO - Mechanical Elements Box | True
4 | M00799 | Spacer M5x9mm | 8.00 | M00172 | EVO - Spacer Bag - M5x9 | False
3 | M00166 | EVO - Spacer Bag - M5x12 | 1.00 | M00174 | EVO - Mechanical Elements Box | True
4 | M00793 | Spacer M5x12mm | 10.00 | M00166 | EVO - Spacer Bag - M5x12 | False
3 | M00167 | EVO - Spacer Bag - M5x15 | 1.00 | M00174 | EVO - Mechanical Elements Box | True
4 | M00794 | Spacer M5x15mm | 5.00 | M00167 | EVO - Spacer Bag - M5x15 | False
3 | M00168 | EVO - Spacer Bag - M5x19 | 1.00 | M00174 | EVO - Mechanical Elements Box | True
4 | M00795 | Spacer M5x19mm | 8.00 | M00168 | EVO - Spacer Bag - M5x19 | False
3 | M00169 | EVO - Spacer Bag - M5x30 | 1.00 | M00174 | EVO - Mechanical Elements Box | True
4 | M00796 | Spacer M5x30mm | 11.00 | M00169 | EVO - Spacer Bag - M5x30 | False
3 | M00173 | EVO - Spacer Bag - M6x90 | 1.00 | M00174 | EVO - Mechanical Elements Box | True
4 | M00800 | Spacer M6x90mm | 4.00 | M00173 | EVO - Spacer Bag - M6x90 | False
3 | M00198 | EVO - V-Wheels Bag - M5 | 1.00 | M00174 | EVO - Mechanical Elements Box | True
4 | M00882 | Wheel with Bearings for V-slot Profile - Type B | 29.00 | M00198 | EVO - V-Wheels Bag - M5 | False
3 | M00063 | Angle Bracket 60 B-Type Groove 8 | 8.00 | M00174 | EVO - Mechanical Elements Box | False
3 | M01680 | EVO - Acrylic Parts - Protection Plate Z | 1.00 | M00174 | EVO - Mechanical Elements Box | True
4 | M00716 | PMMA Sheet 3mm 600x400mm, Light Blue | 0.25 | M01680 | EVO - Acrylic Parts - Protection Plate Z | False
2 | M00195 | EVO - Steel Parts Box | 1.00 | M00201 | EVO-L - Main Box 1/2 | True
3 | M00182 | CNC Evo - Steel Parts - AMB Interface | 2.00 | M00195 | EVO - Steel Parts Box | False
3 | M00187 | CNC Evo - Steel Parts - Foot | 4.00 | M00195 | EVO - Steel Parts Box | False
3 | M00188 | CNC Evo - Steel Parts - Gantry | 2.00 | M00195 | EVO - Steel Parts Box | False
3 | M00191 | CNC Evo - Steel Parts - X-axis Carrier Back | 1.00 | M00195 | EVO - Steel Parts Box | False
3 | M00192 | CNC Evo - Steel Parts - X-axis Carrier Front | 1.00 | M00195 | EVO - Steel Parts Box | False
3 | M00194 | CNC Evo - Steel Parts - Z-axis Plate Top | 1.00 | M00195 | EVO - Steel Parts Box | False
3 | M00193 | CNC Evo - Steel Parts - Z-axis Plate Bottom | 1.00 | M00195 | EVO - Steel Parts Box | False
2 | M00215 | EVO/PRO - Interface Unit | 1.00 | M00201 | EVO-L - Main Box 1/2 | True
3 | M00189 | CNC Evo/Pro - Steel Parts - Interface Unit Base | 1.00 | M00215 | EVO/PRO - Interface Unit | False
3 | M00190 | CNC Evo/Pro - Steel Parts - Interface Unit Cover | 1.00 | M00215 | EVO/PRO - Interface Unit | False
3 | M00011 | 7" LCD Touch Screen 1024x600 TFT | 1.00 | M00215 | EVO/PRO - Interface Unit | False
3 | M00700 | Numeric Keypad 34 Keys | 1.00 | M00215 | EVO/PRO - Interface Unit | False
3 | M01715 | ISO 7380 M3x4 Black Screw | 8.00 | M00215 | EVO/PRO - Interface Unit | False
3 | M00842 | Tooth Lock Washer DIN6798 M6 Type A Black | 8.00 | M00215 | EVO/PRO - Interface Unit | False
3 | M01698 | DIN912 M4x16 Black screw | 2.00 | M00215 | EVO/PRO - Interface Unit | False
3 | M01704 | DIN912 M6x16 Black screw | 2.00 | M00215 | EVO/PRO - Interface Unit | False
3 | M00543 | HDMI Cable Male/Male 1.5m | 1.00 | M00215 | EVO/PRO - Interface Unit | False
3 | M00849 | USB-A Micro USB Cable 1.5m | 1.00 | M00215 | EVO/PRO - Interface Unit | False
3 | M01637 | INT - Fixation Bag | 1.00 | M00215 | EVO/PRO - Interface Unit | True
4 | M01636 | Spacer M6x16 | 2.00 | M01637 | INT - Fixation Bag | False
4 | M01694 | DIN9021 Washer M6x18 | 2.00 | M01637 | INT - Fixation Bag | False
4 | M00556 | I-Type Sliding Nut M6 | 2.00 | M01637 | INT - Fixation Bag | False
4 | M01748 | DIN912 M6x25 Black screw | 2.00 | M01637 | INT - Fixation Bag | False
3 | M00716 | PMMA Sheet 3mm 600x400mm, Light Blue | 1.00 | M00215 | EVO/PRO - Interface Unit | False
3 | M00461 | Disc Magnet Ø 10mm, height 3mm | 3.00 | M00215 | EVO/PRO - Interface Unit | False
3 | M01675 | DIN912 M4x25 Black screw | 2.00 | M00215 | EVO/PRO - Interface Unit | False
3 | M01534 | Male USB-A to Male USB-C Cable 150cm | 1.00 | M00215 | EVO/PRO - Interface Unit | False
2 | M00199 | EVO-L - Electronic Components box | 1.00 | M00201 | EVO-L - Main Box 1/2 | True
3 | M00696 | ALL - Nema23 Motor | 4.00 | M00199 | EVO-L - Electronic Components box | True
4 | M00697 | Nema23 Stepper Motor 5A 6.35mm Shaft | 4.00 | M00696 | ALL - Nema23 Motor | False
4 | M00660 | Micro-Fit 3.0 Male Connector Housing | 4.00 | M00696 | ALL - Nema23 Motor | False
4 | M00662 | Micro-Fit Male Crimp Terminal Contact | 14.00 | M00696 | ALL - Nema23 Motor | False
3 | M00196 | EVO - Mechanical Switch Bag - SPDT-NO/NC | 1.00 | M00199 | EVO-L - Electronic Components box | True
4 | M00651 | Mechanical Switch SPDT-NO/NC | 4.00 | M00196 | EVO - Mechanical Switch Bag - SPDT-NO/NC | False
3 | M01078 | Touch Probe Z Device (3-pins model) | 1.00 | M00199 | EVO-L - Electronic Components box | False
3 | M00482 | Emergency Stop Button 1NC | 1.00 | M00199 | EVO-L - Electronic Components box | False
3 | M00007 | Power Cable C13 IEC to CEE 7/4, Schuko, 2m, 10 A, 250 V | 1.00 | M00199 | EVO-L - Electronic Components box | False
3 | M00848 | USB Key 2Gb | 1.00 | M00199 | EVO-L - Electronic Components box | False
3 | M00384 | ALL - Cable Cover for I-type 6 Profile 330mm | 2.00 | M00199 | EVO-L - Electronic Components box | True
4 | M00383 | Cable Cover for I-type 6 Profile (2m) | 0.34 | M00384 | ALL - Cable Cover for I-type 6 Profile 330mm | False
3 | M01067 | EVO-L - Motor Cables | 1.00 | M00199 | EVO-L - Electronic Components box | True
4 | M00203 | EVO-L - BELRAM lot of Motor Cables | 1.00 | M01067 | EVO-L - Motor Cables | True
5 | M00670 | Motor Cable X 330cm, Red (Evo-L) | 1.00 | M00203 | EVO-L - BELRAM lot of Motor Cables | False
5 | M00674 | Motor Cable Y1 180cm, Green (Evo-M/L) | 1.00 | M00203 | EVO-L - BELRAM lot of Motor Cables | False
5 | M00684 | Motor Cable Z 400cm, Blue (Evo-L) | 1.00 | M00203 | EVO-L - BELRAM lot of Motor Cables | False
5 | M00679 | Motor Cable Y2 390cm, Yellow (Evo-L) | 1.00 | M00203 | EVO-L - BELRAM lot of Motor Cables | False
4 | M00974 | Cable Tie 385mm x 4.8 mm, Blue | 1.00 | M01067 | EVO-L - Motor Cables | False
4 | M00659 | Micro-Fit 3.0 Female Connector Housing | 4.00 | M01067 | EVO-L - Motor Cables | False
4 | M00661 | Micro-Fit Female Crimp Terminal Contact | 14.00 | M01067 | EVO-L - Motor Cables | False
3 | M00202 | EVO-L - Mechanical Switch Cables | 1.00 | M00199 | EVO-L - Electronic Components box | True
4 | M01756 | Mechanical Switch Cable Y2- 210cm, Yellow (Evo-L) | 1.00 | M00202 | EVO-L - Mechanical Switch Cables | False
4 | M00645 | Mechanical Switch Cable X- 330cm, Red (Evo-L) | 1.00 | M00202 | EVO-L - Mechanical Switch Cables | False
4 | M00646 | Mechanical Switch Cable Y1- 140cm, Green (Evo-S/M/L) | 1.00 | M00202 | EVO-L - Mechanical Switch Cables | False
4 | M00650 | Mechanical Switch Cable Z- 410cm, Blue (Evo-L) | 1.00 | M00202 | EVO-L - Mechanical Switch Cables | False
4 | M00974 | Cable Tie 385mm x 4.8 mm, Blue | 1.00 | M00202 | EVO-L - Mechanical Switch Cables | False
3 | M00200 | EVO-L - Timing Belt Bag - GT2 | 1.00 | M00199 | EVO-L - Electronic Components box | True
4 | M00532 | GT2 Timing Belt 6mm 1330 mm | 3.00 | M00200 | EVO-L - Timing Belt Bag - GT2 | False
2 | M00823 | Square Plate - First CNC Test | 1.00 | M00201 | EVO-L - Main Box 1/2 | False
1 | M00222 | EVO/PRO-L - Structure Box 2/2 | 1.00 | M00652 | EVO-L [M0 use] | True
2 | M00055 | Alu Profile V-3030 (240mm) [1x M6 thread on BOTH sides] | 2.00 | M00222 | EVO/PRO-L - Structure Box 2/2 | False
2 | M00034 | Alu Profile I-6030 (1020 mm) | 2.00 | M00222 | EVO/PRO-L - Structure Box 2/2 | False
2 | M00035 | Alu Profile I-6030 (1170 mm) | 3.00 | M00222 | EVO/PRO-L - Structure Box 2/2 | False
2 | M00056 | Alu Profile V-6060 (1230 mm) [4x M6 threads on BOTH sides] | 3.00 | M00222 | EVO/PRO-L - Structure Box 2/2 | False
2 | M00374 | Cable Chain 900mm (Evo/Pro-S/M/L) | 1.00 | M00222 | EVO/PRO-L - Structure Box 2/2 | False
2 | M00372 | Cable Chain 1325mm (Evo/Pro-L) | 1.00 | M00222 | EVO/PRO-L - Structure Box 2/2 | False

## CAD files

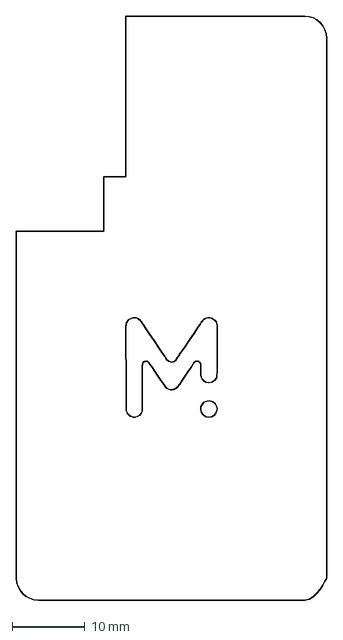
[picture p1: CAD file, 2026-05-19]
cad/EVO Mounting Gauge.dxf
42.5 x 80.0 mm

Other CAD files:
cad/Cable Clip for I-type Groove 6mm.step
cad/EVO-CU V1.0.step

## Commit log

2026-02-12 Initial commit with all current files
    [EVO-CU V1.0.step]
2026-02-12 Update of the BOM: EVO-S V1.0
    SKU: M00654
    File: EVO-S V1.0.csv
    Synced at: Thu Feb 12 13:55:25 UTC 2026
    [EVO-S V1.0.csv]
2026-02-12 Update of the BOM: EVO-M V1.0
    SKU: M00653
    File: EVO-M V1.0.csv
    Synced at: Thu Feb 12 14:15:59 UTC 2026
    [EVO-M V1.0.csv]
2026-02-12 Update of the BOM: EVO-L V1.0
    SKU: M00652
    File: EVO-L V1.0.csv
    Synced at: Thu Feb 12 14:40:18 UTC 2026
    [EVO-L V1.0.csv]
2026-02-18 updated readme with cad previews
2026-03-02 Update of the BOM: EVO-CU V1.0
    SKU: M00148
    File: EVO-CU V1.0.csv
    Synced at: Mon Mar 2 07:56:43 UTC 2026
    [EVO-CU V1.0.csv]
2026-05-19 Added mounting gauge CAD file
    [EVO Mounting Gauge.dxf]
